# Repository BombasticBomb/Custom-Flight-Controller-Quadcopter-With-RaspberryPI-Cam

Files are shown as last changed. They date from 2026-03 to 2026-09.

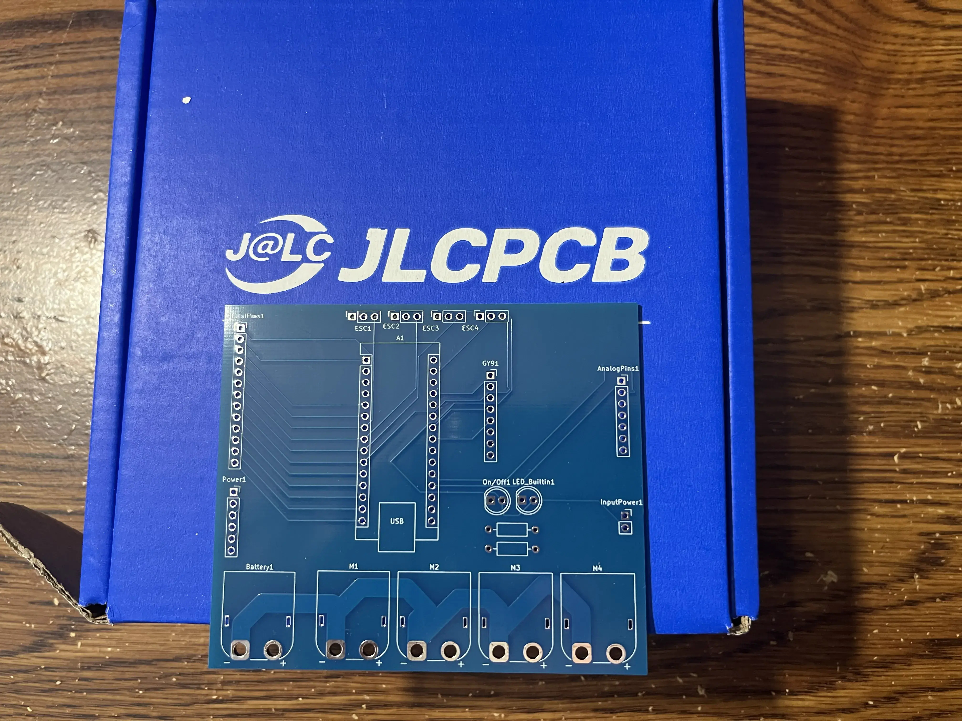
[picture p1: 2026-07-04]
PCB Files/Production/pcb.jpg

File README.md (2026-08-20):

## Custom Drone Flight Controller
Arduino + MPU9250 based Flight Controller for Quadcopter!
This project is a custom-built quadcopter drone that uses an Arduino flight controller with an MPU9250 IMU. Will use a flight controller written in Arduino C++ with a cascaded PID loop for stabilization!
Hack Club Project (Approved): https://stardance.hackclub.com/projects/21695

## 3D Model

This'll be printed in Carbon Fiber Nylon Filament, so it is actually strong enough to be a drone chassis. I will also use a Gyroid infill pattern with 40% infill to make it really strong, and I'll also use a wall count of 6 for further reinforcement. 
parts

## Inspiration
This is my hack club project to build a quadcopter from scratch with a custom flight controller with Arduino &amp; MPU9250. Growing up, I'd watch many science and engineering videos online; I've always been a science kid who spends his time watching astronomy, engineering, etc type videos. I did this project to challenge myself in learning the ins and outs of how a quadcopter actually works, and also to combine my skills in hardware, electronics, and coding to create something unique and not just follow a tutorial.


 ## What Makes This Project Unique
Unlike most custom drones that rely on preprogrammed ready-to-fly flight controllers, my project uses a fully custom flight controller using Arduino & mpu9250 that I had to do a lot of research to actually learn how it works using custom cascaded PID controller loops (and in the future, an extended Kalman filter), and I am working on developing it into a fully functioning firmware. Along with that, I am utilizing a novel method to stream video transmission using a USB camera and the Raspberry Pi using a Python script that uses OpenCV to play video on a web dashboard hosted in Flask and streamed with Flask-socketio. This is a unique method as I offload the low-level control to the Arduino, while I implement advanced features such as a camera (and hopefully in the future GPS, ultrasonic sensors, etc) through the more powerful Raspberry Pi, which actually runs the Linux Operating System.
- Arduino --> Does the low-level flight control and sensor fusion
- Raspberry Pi --> Video Streaming
**Note: Using the onboard wifi on the Raspberry Pi does mean the video transmission range is limited, and beyond that range, we have to rely solely on radio.

## Wiring Diagrams
circuit diagram


| # | Arduino --> MPU9250 | | |
| - | --- | - | --- |
| | **Arduino** | --> | **MPU9250** |
| | 5V | --> | 5V |
| | GND | --> | GND |
| | A4 | --> | SDA |
| | A5 | --> | SCL |

| # | Arduino --> RC Receiver | | |
| - | --- | - | --- |
| | **Arduino** | --> | **RC Receiver** |
| | 5V | --> | 5V |
| | GND | --> | GND |
| | RX | --> | IBus |

| # | Arduino --> ESC | | |
| - | --- | - | --- |
| | **Arduino** | --> | **ESC** |
| | 5V | --> | 5V |
| | GND | --> | GND |
| | 3 | --> | ESC1 |
| | 4 | --> | ESC2 |
| | 5 | --> | ESC3 |
| | 6 | --> | ESC4 |

## Custom PCB:

pcb
Note: The ESCs themselves are part of the wiring diagram and are powered by the Arduino. It is crucial to note the motors themselves, and the Arduino also gets power from the main battery. The reason this configuration was required is that the Arduino converts the 11.1V on the 3S battery to 5V and supplies it to the other electronics.

# Bill of Materials

| Name | Purpose | Quantity | Total Cost (USD) | Link | Distributor |
|---|---|---|---|---|---|
| EVE 50PL 21700 5000mAh 50A Battery | This'll power the drone through its flight. I decided to buy Li-ion batteries and manually connect 3 to make a 3S cell to make a 5000mAh 3S battery pack. This'll help the drone fly longer. I'm buying one extra just in case. | 4 | 24.00 | https://www.18650batterystore.com/products/eve-50pl-21700-5000mah-50a-battery?variant=46405896798359 | 18650 Battery Store |
| JLCPCB Order + Shipping | I'll be manufacturing my custom PCB from JLCPCB. | 1 | 4.30 | https://cart.jlcpcb.com/quote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 | JLCPCB |
| Male & Female Headers | It'll be used to connect things on the PCB. | 1 | 3.82 | https://www.aliexpress.us/item/3256805860047704.html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 | AliExpress |
| XT90 Male to XT60 Female connector for battery | This converts the XT90 on the battery to XT60 so it can be connected to the PCB. | 1 | 1.00 | https://www.aliexpress.us/item/3256809870073827.html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 | AliExpress |
| Drone Frame | This will be the frame that I will be doing all the testing on. I'll have to ship it to my location. | 1 | 5.00 | https://github.com/hackclub/print-legion | Hack Club Legion |
| 1400KV Brushless Motors | These will be the motors that generate lift for the drone. | 4 | 33.40 | https://www.robotshop.com/products/e-s-motor-xxd-a2212-brushless-motor-160w-mounting-base-kits-kv-1400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 | Robotshop |
| Raspberry PI 4 4GB | This will be used to connect the USB camera and for video transmission. I already have this, so I will not need to buy it. | 1 | 0.00 | https://www.centralcomputer.com/raspberry-pi-4-model-b-rpi4-modbp-4gb-4gb-ddr4-ram-bcm2711-soc-usb-3-0-poe-enabled.html | Central Computers |
| Arduino Nano | This will be running the flight software and controlling the motors. I already have this, so I will not need to buy it. | 1 | 0.00 | https://www.aliexpress.us/item/3256809956121978.html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 | AliExpress |
| GY-91 Board with both MPU-9250 & BMP180 | This will the the 9 Axis Flight Controller for the drone (Gyroscope, Accelerometer, Magnetometer, Altometer). | 1 | 6.34 | https://www.aliexpress.us/item/3256810419378175.html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 | AliExpress |
| 8x4.5 Inch RC Drone Propellers | These will be used on the brushless motors to provide lift for the drone. I am buying 8 pieces instead of 4 in case some break during testing. | 1 | 0.92 | https://www.aliexpress.us/item/2251832730802090.html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 | AliExpress |
| 3S Li-po Battery Charger US Plug | This will be used to charge the battery. | 1 | 11.61 | https://www.aliexpress.us/item/3256805934795867.html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 | AliExpress |
| MicroZone MC6C Mini V2 2.4G 6CH Controller Transmitter w/ Receiver | This will be used for the radio communication with the drone. | 1 | 35.24 | https://www.aliexpress.us/item/3256807243819244.html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 | AliExpress |
| 30A Brushless Motor ESC | This will be the Electronic Speed Controller for the 4 brushless motors on the drone. I need to buy 2 pieces for a total of 4 for each motor. | 1 | 12.87 | https://www.aliexpress.us/item/2252799818726193.html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 | AliExpress |
| 12V-5V Buck Converter | This'll convert the 11.1V from the 21700 battery pack to 5V so the Raspberry PI can use it. | 1 | 0.99 | https://www.aliexpress.us/item/3256806059787124.html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 | AliExpress |
| **Total** | | | **139.49** | | |

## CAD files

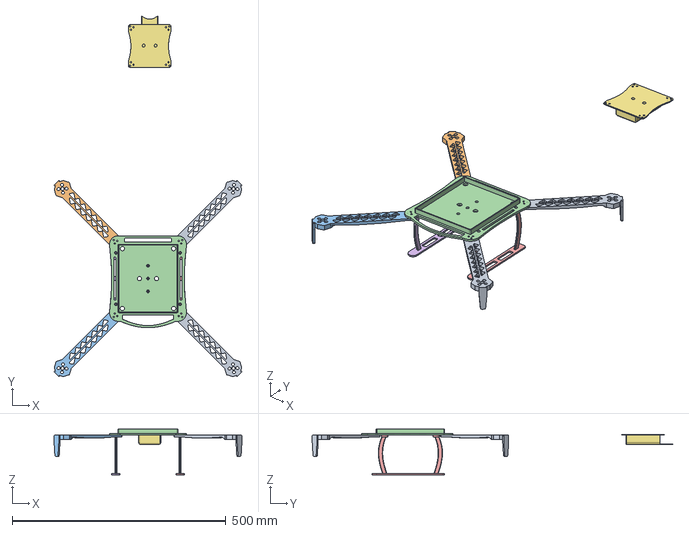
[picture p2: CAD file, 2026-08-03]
CAD/Drone.step
439.9 x 843.9 x 107.0 mm

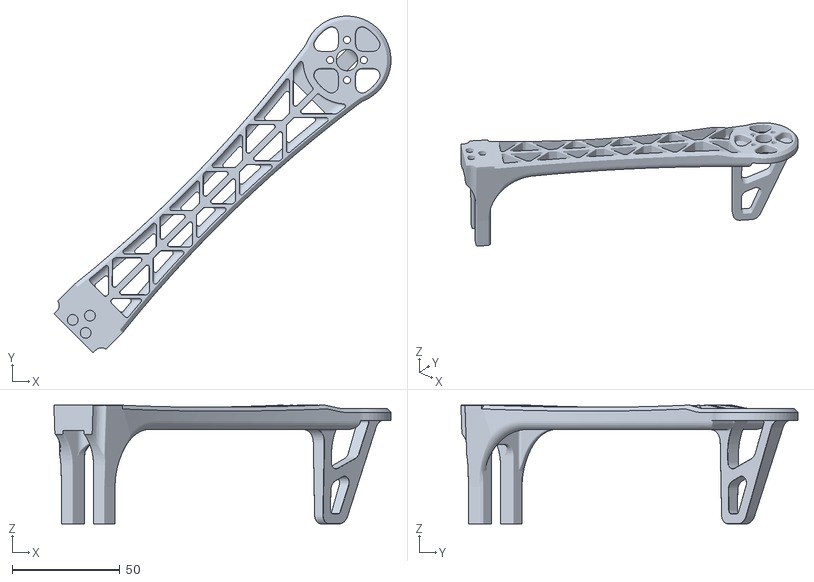
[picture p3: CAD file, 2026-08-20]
CAD/Production/Arm.stl
156.1 x 156.0 x 55.1

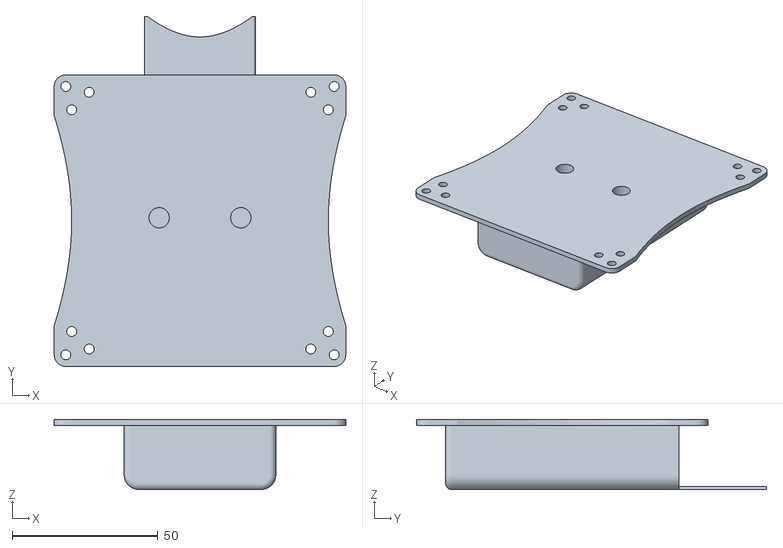
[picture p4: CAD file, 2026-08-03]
CAD/Production/Chassis2.stl
100.0 x 120.0 x 24.0

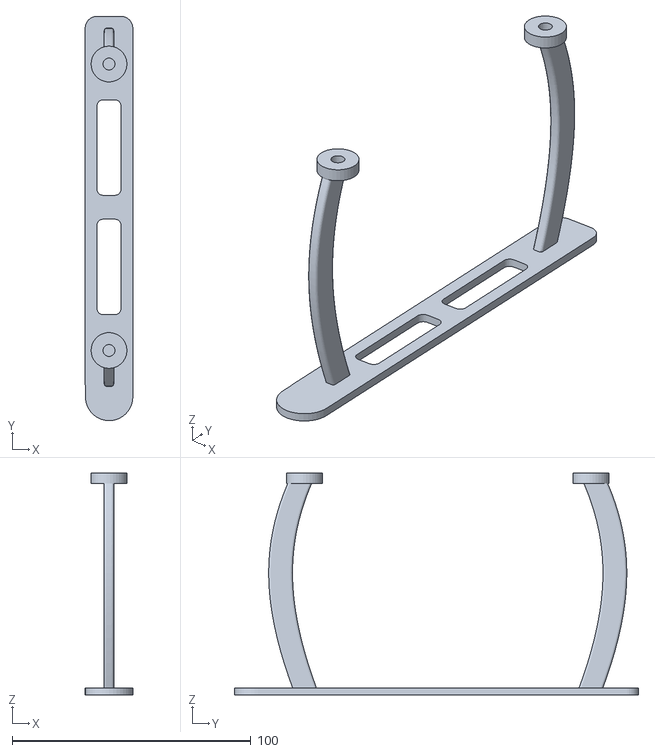
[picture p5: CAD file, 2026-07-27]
CAD/Production/Leg.stl
20.0 x 169.4 x 93.0

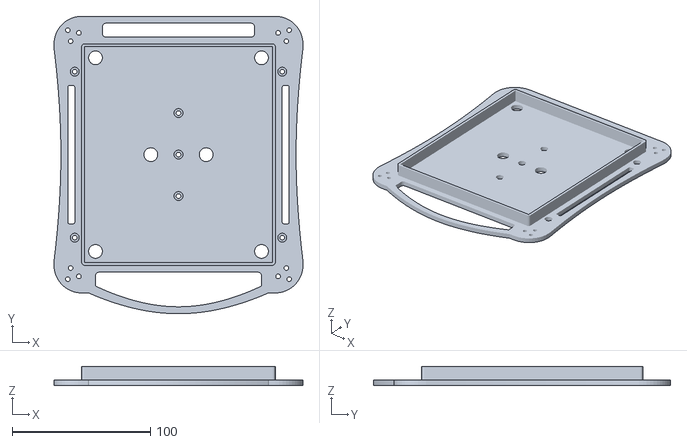
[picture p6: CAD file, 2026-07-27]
CAD/Production/Chassis.stl
180.0 x 215.0 x 14.0

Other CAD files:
CAD/Drone.f3d

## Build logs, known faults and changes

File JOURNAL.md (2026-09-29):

# 9/28/2026 10:32 PM - Setting up F450M Chassis to test brushless motors.

_Time spent: 1h 21m_

Ok, I'm back working on the drone after over a month, I was kinda busy with schoolwork. Anyways, I haven't gotten to test the new arm design, and I called up the printlegion supplier of mine and got a new order going. In the meanwhile, I decided to continue trying to work on the drone with a spare F450 drone chassis kit I had. Not only that, since all my propellers broke last time - lots of work done in this after school session.



Firstly, I screwed together the F450 chassis, unscrewed the motors from my custom chassis and put them on the F450 arms, and it came out as the generic drone everyone builds. Anyways, I also wanted to test if the motors had any thrust imbalances that was causing any problems, as since I crashed the drone a couple of times during previous testing sessions, I feared the motor shafts may have bent. Therefore, this test can validate the motors with a tried and tested chassis before I go back to my original chassis.



After that, I obviously attached the new propeller sets I got. Before I was testing out in the roads on concrete, so each crash ended up breaking 1 or 2 propellers. So, this time I not only got new stronger propellers that had a larger pitch and a stronger mid-section, I am also thinking of doing all my testing in the grassy area nearby, so hopefully no more propellers will break.



Lastly, I am realizing the cascaded pid loop I am running on the arduino may be too slow, as the arduino is not a very powerful microcontroller. So, my next target is now an ESP32, as the advanced control features I want to implement needs a stronger processor. Not only that, the ESP32 also has a built-in FPU, which should make my PID calculations much faster. But before I start migrating my code however, I again want to test my motors, and so for now I decided to test the drone with ESP-FC, an open source drone firmware for ESP32 that is configurable with betaflight configurator.



I flashed it and got betaflight configurator running, but I didn't get any chance to set up the pins. One advantage of using ESP32 is that it has hardware interrupts on many GPIO pins, and it can also use the SBUS protocol my receiver uses instead of individual PWM channels. Next session I'll set up all the pin connections, PID tune betaflight, and hopefully there'll be no problems with my motors.

# 8/19/2026 8:39 PM - Designing New Arm.

_Time spent: 54m_

Today I decided to tackle the problem of designing a completely new arm for the drone. As I already mentioned before, the arm keeps getting bent from the thrust and also the weight of the drone, meaning I'd need to make it stronger and more stiff so it doesn't bend.


So I started designing, but since I was designing on a pretty cluttered design file and my arm was built up with work over many days, what I designed was not something I particularly liked.

This project was getting more time-consuming and expensive than it ever needed to be, and it was getting bad. I struggled with this for like about 30 minutes, but I couldn't find ways to quickly make it better, and now that school had started I didn't have time like before to iterate and reprint quickly.
So, I took a shortcut, I had to...

I decided that in order to save time, atleast for the arm, I'd go with the tried and tested DJI F450 arm design, and make some small designs to make it work with my specific chassis.
Using the holes from my chassis, I cut those holes into the new arm design so I can attach it with M3 screws to the main chassis.
Therefore, credits to Sarthak Nashirabadkar on GrabCAD for the arm design, it really helped me to quickly get this project back on its feet.
Link: https://grabcad.com/library/f450-quadcopter-drone-frame-1



Additionally, I also made another small attaching thing in case someone want to use actual DJI F450 arms, and just 3D print their chassis, and so for that reason I made a small adapter to attach that arm to my chassis.


Lastly, I also made the legs of the drone a little thicker, as the last time I printed it they were way too thin and broke on the first day.


# 8/18/2026 8:34 PM - Testing 1st Flight (Failed).

_Time spent: 1h 37m_

Today I tried to do my first test run. Firstly I connected up the propellers and saw if the motors spin properly. Then, I went in and tried to see if the drone could stabilize with my code.


Then, I tried to test run it on a weight I had lying around to see if it could stabilize. But no matter what, it just won't stabilize. The drone would like shake up and down for some reason on both sides.

So then I tried tweaking the values by increasing the rate pid constants and decreasing the angle one. It didn't help much. 

So, I tried installing ESP-FC on my ESP32, which is a community made ready-to-fly flight controller, to just see if there's something seriously wrong with my hardware.

Due to the ESP-FC being reall good firmware the drone was able to stabilize better, but it seems like my arms were getting bent by the sheer weight and the thrust. Apparently it was a structural issue all along!


Therefore, I decided to not waste any more time on this drone and get back to designing. I'll be soon designing a new drone arm and getting that printed, and hopefully this time it'll be much thicker and do fine.


# 8/11/2026 6:46 PM - Assembling The Parts.

_Time spent: 1h 07m_

I finally got the 3D printed chassis parts for my drone, and I wasted no time and got to work assembling it. Here's some individual photos.



I used M3 screws, bolts and washers. The arms are a bit loose, but we'll see.

# 8/1/2026 4:36 PM - Redesigning Drone Mounting Holes

_Time spent: 2h 05m_

I was hesitant to print the drone arm without testing them with the actual motor first, so I printed one.



However, I soon realized that even though from google I found that these motors have a mounting pattern or 16mmx19mm, the actual dimensions were definitely off on my specific motor brand, as I couldn't get it to fit at all. The holes had also shrunk due to the printing layers.


After some back and forth on my Ender 3 Pro, I realized the best dimension was actually 12.7mm x 13.5mm, which is wildly different from the actual one. Anyways, I also decided to use a custom hole and not the designated M3 hole in fusion 360, and I'll just use washers to make sure the screws stay where they are and look clean.




And, it finally worked!



# 8/1/2026 4:36 PM - Updating PID Controller to Cascaded PID Loop

_Time spent: 3h 03m_

First of all, it seems like I got scammed on the GY-91 chip I bought from Aliexpress, cause the chip returns a WHO_AM_I address of 0x70, which is the address of the MPU6500, not the MPU9250 I ordered. I did some more research, and it seems like these chinese sellers often put those chips and call it MPU9250. Thus, I won't be able to use a magnetometer to correct yaw drift, but hopefully I'll buy a good proper IMU from Adafruit or something, but that'll be for a future upgrade when I also move to the ESP32.

Anyways, I went on and implemented a cascaded pid loop in my code. The inner loop is faster and controls angular velocity, which keeps the drone stable. In my code, I allowed the inner loop to run as fast as possible, and then the outer loop runs. My overall loop has a set HZ rate of 500HZ, but let's see if the Arduino can actually run that fast.



Sadly to add on to my problems, I also got stuck with the issue that the Mahony filter didn't work no matter what I did. Since I didn't read into the implementation of the filter in the library, and it'll be too complicated, I decided to switch back to a complementary sensor fusion algorithm. I took 95% from the gyroscope, and 5% from the accelerometer. It won't have noise correction, but I think it'll do for now. And obviously I don't have any yaw correction. 


For the angles from the accelerometer, I used atan2 function to get the angles, and in the code I didn't use g and rather took the vector of the az and ay component using pythagorean theorem. Originally I thought I could use gravity g, but since the drone experiences g forces we can't use it.


For the Gyroscope I took the rates in radians, converted them to degrees by multiplying them by 180/pi, and then took the current angle and to that I added the Gyro rates multiplied by dt, essentially integrating the gyro rates over time to get the angles. This was done in the complementary filter.


To correct gyro bias, I made a small section of code to sample the gyroscope a set amount of times, for example 4000 samples, and average them and subtract them from the gyroscope data to find the true angles, or as close as possible. With this however, it adds a 1-2 second delay to the startup time, but I think it's definitely worth it as now the Gyroscope will adjust and calibrate no matter what happens to the drone structurally.


Lastly added some flight mode code and a flight variable so the drone knows whether its in flight mode or not.


In the next part of the code I'll probably try to replace the ServoTimer2 library with my own implementation of PWM signals, as it may cause problems because of the pin timer. Also after I get the frame I also have PID tuning to do.

# 8/1/2026 1:25 PM - Soldering the Drone Battery

_Time spent: 3h 13m_

Confident after soldering the last batch of batteries. I decided to start soldering the RS50 Reliance batteries I bought for the actual drone. It started of really rough, with me burning my hands a couple times. So I tried like last time to not use flux, which improved a little bit, but not enough to make it work. Then, I finally ran out of solder, which made me open my new pack of solder I bought. And miraculously, the solder started working. I realized that this new solder had a flux core, which made my life way more easier, and I was able to finish soldering all the batteries.

I hooked it up to my Arduino and ESC, and it was providing nice power.



Just to be sure, I also measured the voltage of the batteries, and since they were almost fully charged, they showed 12.3V, which is normal for a 3S cell.


I also connected it to the smart charger after attaching the load balancing wires, and the 3 cells were all charging normally.


# 7/27/2026 3:40 PM - Designing a second low-profile Chassis for Drone.
I wanted to add a smaller low-profile chassis for the drone if I ever fly it with no big landing legs or payload or cameras, and so I designed another chassis that I'll also manufacture soon.




# 7/24/2026 10:58 PM - Soldering 1st batch of batteries.

_Time spent: 2h 26m_

Today, my order from 18650 battery store for 3 21700 Li-ion cells came in. These are very beefy cells with a max pulse current of 70A and 5000mah capacity, so should be more than enough for my drone project. 

But, since I've never soldered batteries together before and I can't afford a spot solder right now, I decided to test solder on some old 18650 cells I had, and that's what I did.

Overall, it started off pretty rough as the solder was not sticking to the ends of the cells no matter what I tried. Then, i figured that it worked better if I didn't use any flux, which'd to me was counterintuitive as flux makes the solder stick. But anyways, I tried without and managed to solder all the wires together, and it gave me a nice 12V on the 3S cell.

To interface with the smart charger I also bought, I also attached a 4 pin connector to the battery for load-balancing smart charging. Overall it works great and the charger can individually tune the voltages of each cell for protection.


Hopefully in the next log I'd be able to finish soldering the actual 21700 cells to make another, much beefier pack that I'll actually use on the drone. This was for first-time practice and getting to actually know how its done!

# 7/23/2026 7:29 PM - Added Secondary Landing Legs.

_Time spent: 3h 21m_

Firstly, I decided to write the Motors mixer function for the drone with a standard Quad X setup, so I can just call it in the main loop and it'll update the motor values on each iteration according to the PID values.



Then, I write a simple PID function that I'll be using in the main loop. This is not yet a cascaded PID controller, but it's a start. I made some state variables and wrote the function to add up the proportional, integral and derivative part.


To then feed data into the PID function, I used the BolderFlight Invensense Arduino library to interface it with the MPU9250, and get all the data.



All IMU sensors have noise in the data, but since an Arduino is a relatively weak microcontroller running at only 16Mhz, I decided to use a light filter called a Mahony filter, and used the MahonyAHRS library to implement it in my code. If i ever upgrade the flight controller hardware, I'll then manually implement a Extended Kalman Filter, but right now it is too expensive for the Arduino.


I also decided to set the PID loop at a 500Hz rate, which is also how I calculated dt in my code.


Finally, I made a PID controller for each axis of the drone and ran the mixer function at the end of the loop. Also made it that the integral portion will go to 0 when the drone is on the ground to prevent integral buildup when the drone is stationary.


# 7/21/2026 11:34 PM - Added Secondary Landing Legs.

_Time spent: 57m_

I added some small DJI Mini style landing legs to the drone, so that if I ever want I can take the big landing legs off and just have a low profile setup.




# 7/20/2026 10:28 PM - Started writing code to interface the Arduino with the RC transmitter.

_Time spent: 2h 47m_

Firstly, I decided to do some research about the channel configuration and how to read PWM signals from the receiver. Originally, I thought I was going to use the IbusBM library, but apparently my receiver didn't support it.


To solve this problem, I thought I'd use Arduino Nano's hardware interrupts, but the Nano only had 2 pins, and I needed a minimum for my 4 channels: Throttle, Pitch, Yaw, and Roll. Then, I found out about something called pin change interrupts, but those required manual memory address and pin registry configuring, and thankfully the Arduino PinChangeInterrupt library took care of that for me.


Not only that, but I also found out that RC transmitters like these don't have perfect PWM signal outputs, as I measured with the arduino. To fix that and scale it to the perfect 1000um-2000um range needed for the ESCs to work well, I decided to log the range of values that each of the 4 channels output, and used the arduino map() function to scale it to the desired range and constrained it with the constrain() function. This worked remarkably well and I tested it with a Brushless motor and it worked well.



# 7/19/2026 18:03 PM - Completely changed the thickness of parts as Carbon Fiber Nylon is strong enough, and added many decoration holes and patterns to vastly reduce weight.

_Time spent: 3h 19m_


I added these design holes found in other drone chassis kits that not only made it look nicer, it reduced a lot of weight without making the arms that much weaker, as carbon fiber is a very strong material. This reduced the weight of the individual arms from 37g to 25g, as per the printing settings I used. 


Also added some cutouts to the chassis that didn't drastically reduce weight, as the chassis is relatively thin. However, this'll allow me to tie things onto the drone if I ever need to do so in the future, and it also looks nice on the drone chassis.


Similarly, added cutouts to the bottom legs and thinned the pads out a bit too to reduce weight. This resulted in almost 50g of weight reduction.

chip
I was having anxiety about flexing where the motor attaches to the arms, so I made it thicker at just that part. I also added a smooth hilly part that should make it really strong.

# 7/16/2026 9:38 PM - Added Superior Landing Legs & Added Extra Mounting Holes (Future Development)

_Time spent: 2h 34m_


I added 2 extra mounting holes so I can add on new modules in the future for items like Gimbal Camera, GPS, Drop mechanism, etc.


The previous landing leg design had a center of gravity that was relatively high, and standing on tiny legs with little surface area. This design fixed it by making the legs shorter, and adding a smooth pad at the bottom
that'll also be reinforced with shock absorbing foam. Even added some tall standoffs on the arms that may or may not allow me to completely take of the landing legs and land on those!

# 6/26/2026 10:25 PM - Switched Flight Controller From MPU6050 to MPU9250

_Time spent: 21m_


Updated Flight Controller Code for MPU9250 Since I previously tested and wrote code with a MPU6050 because I physically had the sensor, I now decided to update the code to the new and more advanced 
MPU9250. Today’s session was mostly about getting the sensory data (Roll, Pitch, Yaw) from the sensor, and I haven’t implemented a PID loop yet, and I’ll focus on that next, as well as implementing the 
connections from the custom PCB.


# 6/19/2026 1:30 PM - Added Smooth Underside to the Arm and added Electronics Housing

_Time spent: 22m_


I made the arms of the drone thicker so it is more resistant to crashes, which may happen quite a bit during initial PID tuning and testing.

Not only that, I also added a small cutout on the top to house the main electronics, including the battery, the Raspberry PI, and also the custom PCB.


# 6/11/2026 9 PM - More changes to the 3D model of the Drone

_Time spent: 1.5h_

Today, I completely redesigned the chassis of the drone to better suit my needs, as the previous one was too small.


Kept the drone mounting holes the same for the brushless motors, but for simpler building also added screw holes for the 4 arms to attach to the main body.

Also further tweaked the brushless motor part.


In the bottom, added landing legs to provide better stability.



To house the electronics, I added a small area on the top to hold the parts.


# 6/10/2026 10 PM - Designing New Drone Chassis

_Time spent: 2.5h_

In this session, as per the instructions, I decided to make a more stable version of the drone, and this time, it will be fully 3D printed in carbon fiber instead of aluminium to save costs. Since my 3D printer can't print carbon fiber, I will be using Hack Club PrintingLegion. 

For the main drone body, I took inspiration from this YouTube video. 
Link: https://www.youtube.com/watch?v=jeBfLHX1kos&t=72s

However, that'd not fit my requirements, so I will also be adding proper M3 holes and a through-hole for my Bushless motors, and this video helped a lot.
Link: https://www.youtube.com/watch?v=4bDNXpWQaW4


Lastly, I think I'll make some more changes to the drone to make it even sturdier, like adding some pressure absorbers at the bottom of the legs.

# 4/18/2026 6 PM - Finish Designing Custom PCB

_Time spent: 2.5h_

While I was working on the PCB, I decided it's out of my scope to use bare metal chips for the sensors, so in order to improve electronic noise and have a better chance of the PCB working, I decided to switch out the sensor chips for modules. 

Also, due to size constraints, I decided to go with Arduino Nano instead of the big Arduino UNO, as it better fits the PCB. For future developments, I also added lots of header pins connected to the digital and analog pins on the Arduino, so I can expand my capabilities in the future. Similarly, I also added some power pins to power those sensors.

Lastly, I made the PCB and made all the traces. I went with thicker 4mm traces for the Motor power distribution, as more current will flow through them, and everything else with normal 0.025mm traces.

Here's the final PCB:


# 4/7/2026 3 AM - Flight Controller PCB V1

_Time spent: 2h_

I decided to start working on a custom PCB because, without it, the complexity isn't high enough. This is my first time making a custom PCB, so I gave it my best shot :)


I decided to use KiCad for this, and I used bare chips instead of modules for now. Apparently, there are a lot of issues with electronic noise for quacopter PCBs, so I had to do a lot of research on where and how to place components. And, for better sensor readings, I also had to put a 10K resistor, decoupling capacitors, and a MOSFET for level-shifting.


Still not sure whether I will continue this setup, as the electronic noise is a big deal. Might end up switching that out for the GY-91 module itself.

# 3/23/2026 3 AM - PID Loop V1 (Stabilization)

_Time spent: 1h_

In order for a drone to be stable, it needs a feedback loop system that constantly tries to keep it stable, thus keeping its angle 0*. One industry standard way is to implement a PID loop. A PID loop consists of 3 different parts: the proportional, the integral, and the derivative, and the PID controller is the sum of all these 3 controllers. I plan to create a PID controller for each dimension of the drone.

Source: https://en.wikipedia.org/wiki/Proportional%E2%80%93integral%E2%80%93derivative_controller

After some research on YouTube about how a PID controller works, I tried creating my own loop in the stabilization part of my firmware and called the stabilize() function which has the controller. As of right now, I don't have much of an idea as to how the motors behave and how much thrust increases as I increase speed in percentage, so I just made it increase and decrease thrust based on the values from the PID loop. When I actually build the physical drone, it'll have the PID constants tuned, and I'll also tune the thrust increase/decrease for optimal flight.


# 3/19/2026 4 AM - Basic Gyroscope & Accelerometer Sensor Fusion along with Throttle Control

_Time spent: 3.5h_

After choosing the parts for the drone, I decided to start working on the flight controller. In my previous journal logs, I've already shown getting the gyroscope roll, pitch, and yaw values, but as I learned during my research, the gyroscope is subject to drift. The solution - fusing data from the gyroscope along with roll and pitch values gained by integrating the angular velocity given by the accelerometer to get angles, with the gyroscope contributing 98%, while the accelerometer 2% for corrections.


The yaw values cannot be corrected as it would require a magnetometer, which I will use in the final build by replacing the MPU6050 with an MPU9250. 


I also started writing code for reading signals from the radio receiver and its corresponding actions on the motors, which I've defined as servos in the code.
Channels



# 3/18/2026 4 AM - Designing 3D Model of Drone

_Time spent: 2h_

In the past 2 hours, I designed the basic 3D outline of the drone in TinkerCAD to be approved by Hack Club. I chose the parts that I will be using and looked for 3D models online, and if I found them, I used them in the design. Otherwise, I tried to mimic the actual part with TinkerCAD shapes and labels. Things to note: this may be subject to change as I build the project and make important decisions.


If looking for my 3D model to review and approve my project, please look in the releases section. Due to the large file size of the .step file when extracted from the original STL file, it had to be uploaded to releases. 


# 3/17/2026 9 PM - Deciding Propeller, Motor & Battery Sizes

_Time spent: 3h_

In this session, I finished researching the different configurations for the drone and chose the most efficient for my purpose. I decided to stick with 1400kv Brushless motors for a good balance between speed and efficiency, and chose 4 pieces to buy on Amazon.

Then, I chose a 4000mAh 3S Li-po battery for a good flight time and also 4 30A ESCs separately for a better price. Ended up with an 8x4.5 propeller size for the final drone.

Finally, started working on choosing a frame for the drone. I am not sure whether I should buy a frame or print one on my 3D printer, but let's see.

Considering this one:

Source: https://www.printables.com/model/250067-drone-frame

# 3/17/2026 4 AM - Choose Parts

_Time spent: 2.5h_

In the last 2 and a half hours, I brainstormed ideas as to how to build the drone in real life, and decided to choose electronics parts for each job. I decided to go with 1400KV brushless drone motors along with 30A ESCs, along with a radio controller and transmitter for communication. I decided to build a custom IMU with Arduino and MPU6050, and I haven't decided yet on how to build the structural part of the drone. I also started tinkering with the MPU6050 to start building the PID controller for the IMU. 





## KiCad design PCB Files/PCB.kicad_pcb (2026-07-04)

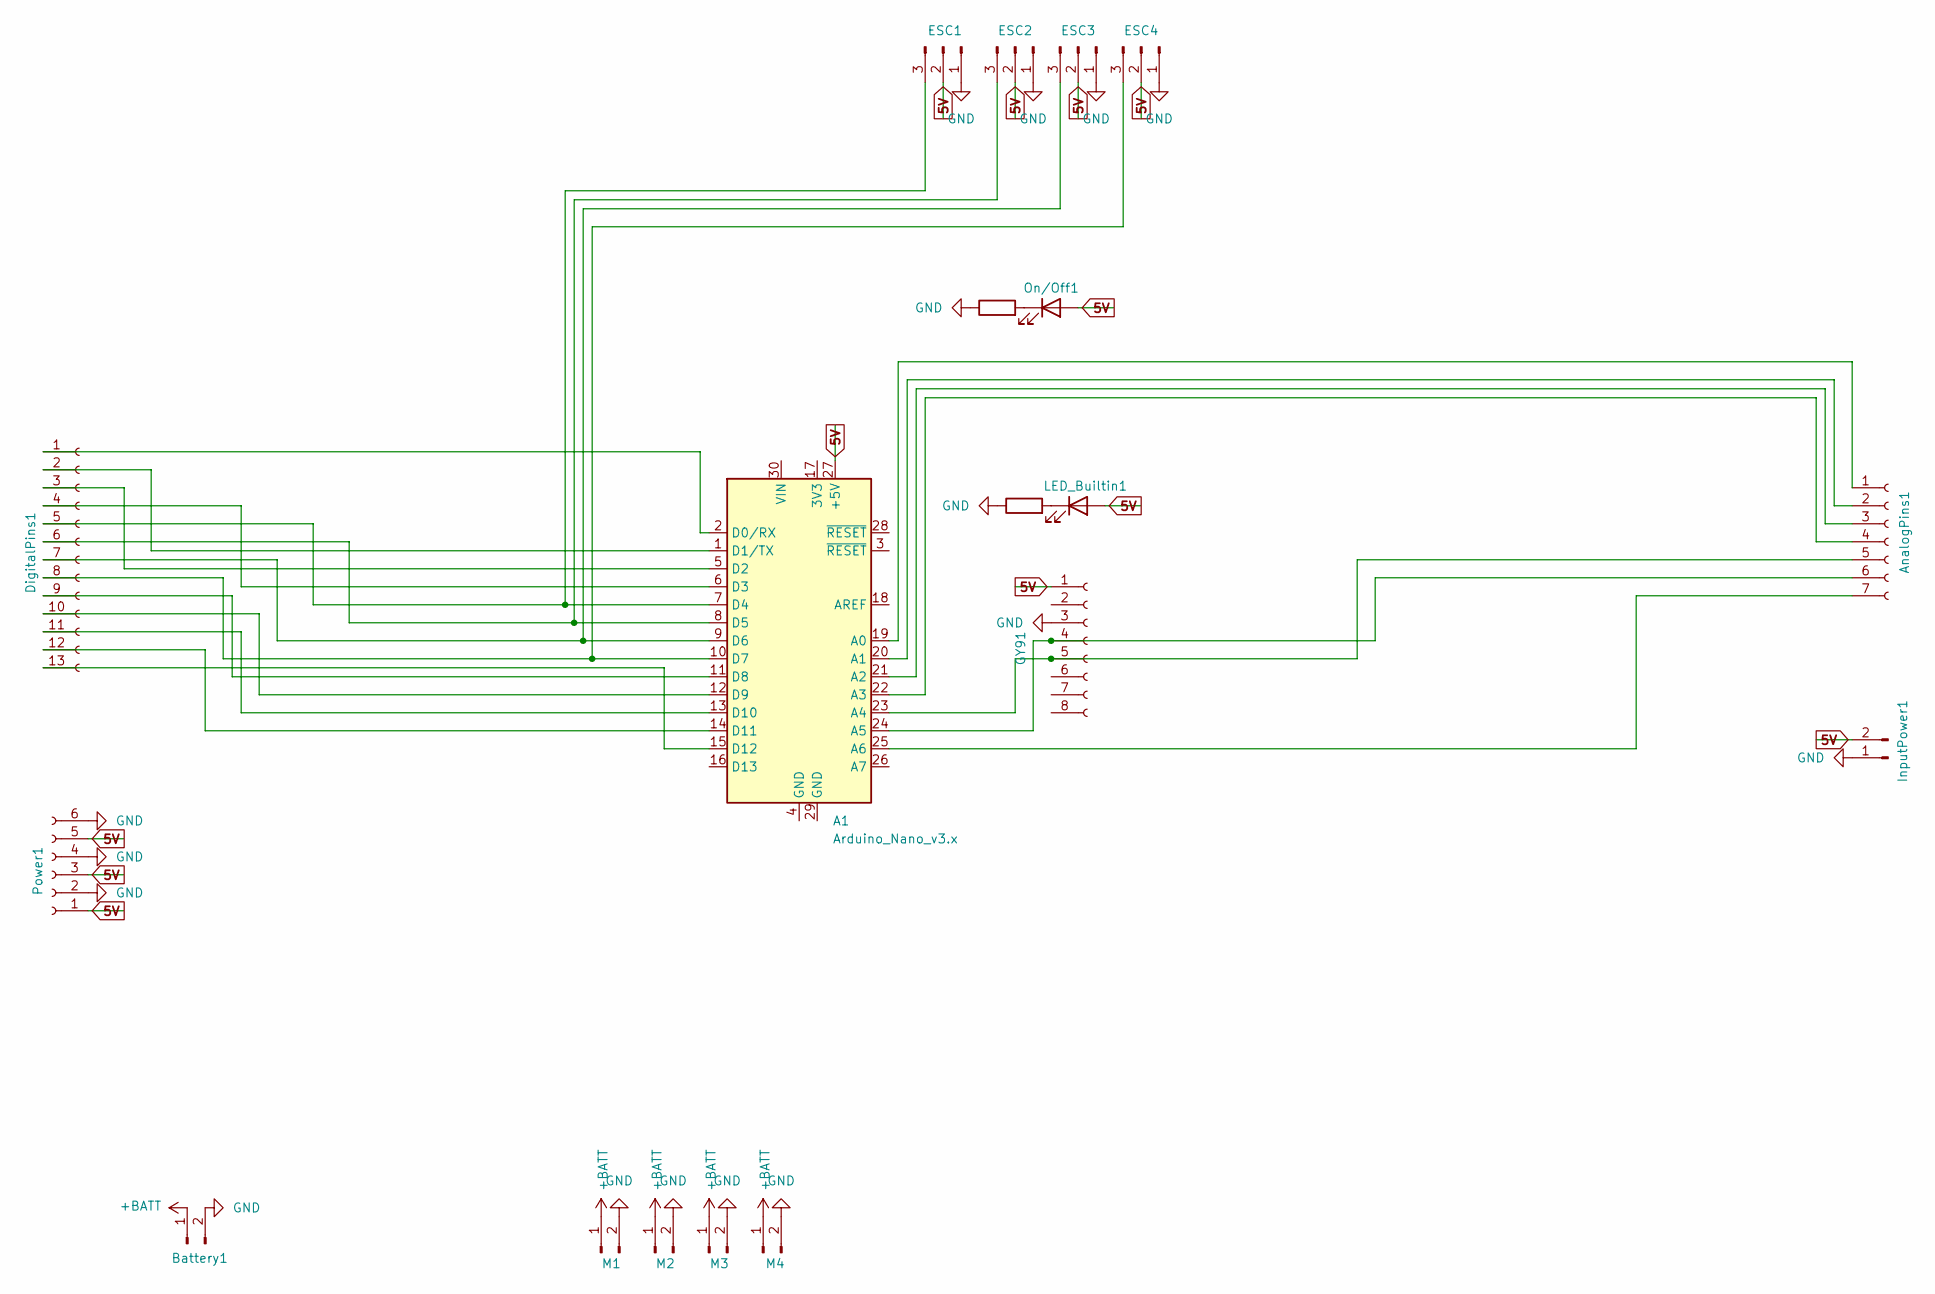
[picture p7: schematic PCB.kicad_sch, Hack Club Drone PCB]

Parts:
A1: Arduino_Nano_v3.x; Arduino_Nano
AnalogPins1: Conn_01x07_Socket; PinSocket_1x07_P2.54mm_Vertical
Battery1: Conn_01x02_Pin; AMASS_XT60PW-M_1x02_P7.20mm_Horizontal
DigitalPins1: Conn_01x13_Socket; PinSocket_1x13_P2.54mm_Vertical
ESC1, ESC2, ESC3, ESC4: Conn_01x03_Pin; PinSocket_1x03_P2.54mm_Vertical
GY91: Conn_01x08_Socket; PinSocket_1x08_P2.54mm_Vertical
InputPower1: Conn_01x02_Pin; PinSocket_1x02_P2.54mm_Vertical
LED_Builtin1: LED; LED_D5.0mm
M1, M2, M3, M4: Conn_01x02_Pin; AMASS_XT60PW-M_1x02_P7.20mm_Horizontal
On/Off1: ON/OFF; LED_D5.0mm
Power1: Conn_01x06_Socket; PinSocket_1x06_P2.54mm_Vertical
R220-1, R220-2: 220; R_Axial_DIN0207_L6.3mm_D2.5mm_P10.16mm_Horizontal

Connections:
5V: A1.27 (+5V), ESC1.2, ESC2.2, ESC3.2, ESC4.2, GY91.1, InputPower1.2, LED_Builtin1.2 (A), On/Off1.2 (A), Power1.1, Power1.3, Power1.5
+BATT: Battery1.1, M1.1, M2.1, M3.1, M4.1
GND: Battery1.2, ESC1.1, ESC2.1, ESC3.1, ESC4.1, GY91.3, InputPower1.1, M1.2, M2.2, M3.2, M4.2, Power1.2, Power1.4, Power1.6, R220-1.1, R220-2.1
unnamed: A1.19 (A0), AnalogPins1.1
unnamed: A1.20 (A1), AnalogPins1.2
unnamed: A1.21 (A2), AnalogPins1.3
unnamed: A1.22 (A3), AnalogPins1.4
unnamed: A1.23 (A4), AnalogPins1.5, GY91.5
unnamed: A1.24 (A5), AnalogPins1.6, GY91.4
unnamed: A1.25 (A6), AnalogPins1.7
unnamed: A1.2 (D0/RX), DigitalPins1.1
unnamed: A1.1 (D1/TX), DigitalPins1.2
unnamed: A1.5 (D2), DigitalPins1.3
unnamed: A1.6 (D3), DigitalPins1.4
unnamed: A1.7 (D4), DigitalPins1.5, ESC1.3
unnamed: A1.8 (D5), DigitalPins1.6, ESC2.3
unnamed: A1.9 (D6), DigitalPins1.7, ESC3.3
unnamed: A1.10 (D7), DigitalPins1.8, ESC4.3
unnamed: A1.11 (D8), DigitalPins1.9
unnamed: A1.12 (D9), DigitalPins1.10
unnamed: A1.13 (D10), DigitalPins1.11
unnamed: A1.14 (D11), DigitalPins1.12
unnamed: A1.15 (D12), DigitalPins1.13
unnamed: LED_Builtin1.1 (K), R220-2.2
unnamed: On/Off1.1 (K), R220-1.2

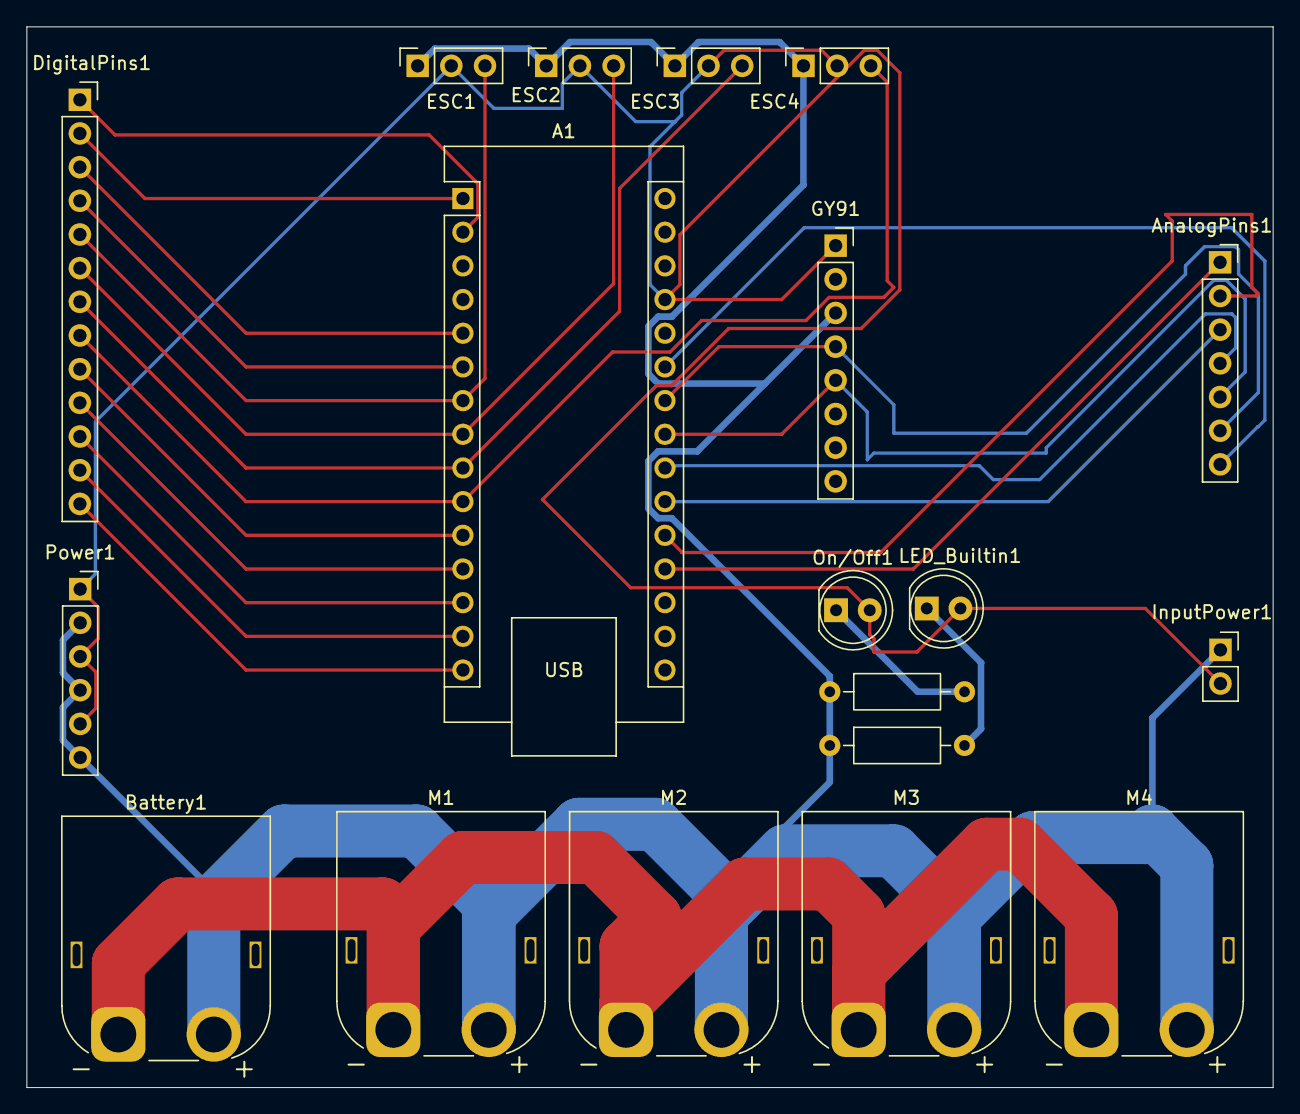
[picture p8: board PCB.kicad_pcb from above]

Board: 2 copper layers, 94.0 x 80.0 mm, 19 parts (0 on the bottom side), 25 nets.

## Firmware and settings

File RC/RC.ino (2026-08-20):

/*
 *Throttle - (944,1944)
 *Pitch - (1196,1694)
 *Yaw - (1248,1752) 
 *Roll - (1296,1800)
 
 *Throttle = Up or Down (Channel 3)
 *Pitch = Forward or Backward (Channel 2)
 *Yaw = Rotation (Channel 4)
 *Roll = Left or Right (Channel 1)
 */

#include "PinChangeInterrupt.h"
#include <Servo.h>
#include "mpu6500.h" //I got fucking scammed so i now gotta use mpu6500 instead of mpu9250!!!

//Flight state variables
bool flight = false;
char flightMode;
float maxFlightSpeed = 0;

//Variables
const int throttlePin = 2; volatile unsigned long throttlePWMStart = 0; volatile int throttleTemp = 1000; 
const int pitchPin = 3; volatile unsigned long pitchPWMStart = 0; volatile int pitchTemp = 1000;
const int yawPin = 4; volatile unsigned long yawPWMStart = 0; volatile int yawTemp = 1000;
const int rollPin = 5; volatile unsigned long rollPWMStart = 0; volatile int rollTemp = 1000;
int minPWM = 1000; int maxPWM = 2000;
int minTilt = -20; int maxTilt = 20; //Tilting of the drone
float currentPitchAngle = 0.0; float currentYawAngle = 0.0; float currentRollAngle = 0.0;
float ax; float ay; float az; float gx; float gy; float gz; float mx; float my; float mz;

//Loop frequency regulation
float loopRate = 500.0; //Loop rate in Hertz (Hz)
const unsigned long refreshInterval = 1000000 / loopRate; // 2000 microseconds
unsigned long previousMicros = 0;

//MPU9250 & BMP280
int imuCSPin = A0;
int bmpCSPin = A1;
bfs::Mpu6500 imu(&SPI, imuCSPin);

//Transmitter Ranges
int throttleStart = 944; int throttleEnd = 1944;
int pitchStart = 1196; int pitchEnd = 1694;
int yawStart = 1248; int yawEnd = 1752;
int rollStart = 1296; int rollEnd = 1800;

//---PID Variables---
//Pitch Angles & Rate Varibales
float pitchAngleKp = 2.0f; float pitchAngleKi = 0.00f; float pitchAngleKd = 0.0f;
float pitchAngleIntegral = 0.0f; float pitchAngleLastError = 0.0f;
float pitchRateKp = 1.0f; float pitchRateKi = 0.00f; float pitchRateKd = 0.0f;
float pitchRateIntegral = 0.0f; float pitchRateLastError = 0.0f;
//Roll Angles & Rate Variables
float rollAngleKp = 2.0f; float rollAngleKi = 0.00f; float rollAngleKd = 0.0f;
float rollAngleIntegral = 0.0f; float rollAngleLastError = 0.0f;
float rollRateKp = 0.75f; float rollRateKi = 0.00f; float rollRateKd = 0.0f;
float rollRateIntegral = 0.0f; float rollRateLastError = 0.0f;
//Yaw Angle 
float yawAngleKp = 0.5f; float yawAngleKi = 0.00f; float yawAngleKd = 0.0f;
float yawAngleIntegral = 0.0f; float yawAngleLastError = 0.0f;
//Storage variables
const float dt = 1.0 / loopRate; int pidPitch = 0; int pidYaw = 0; int pidRoll = 0;
const float pidPWMMin = -450; const float pidPWMMax = 450;

//Sensor fusion variables
float gyroPitch = 0; float gyroYaw = 0; float gyroRoll = 0;
float accelPitch = 0; float accelRoll = 0;
float radToDeg = 57.2957795f; 
float gxBias; float gyBias; float gzBias;
float axBias; float ayBias; 
const int numSamples = 4000; //Bias correcting samples
int successfulSamples = 0;

//Define Motors
Servo esc1; int esc1Pin = 6;
Servo esc2; int esc2Pin = 7;
Servo esc3; int esc3Pin = 8;
Servo esc4; int esc4Pin = 9;
bool motorsEnabled = true;


void setup() {
  Serial.begin(115200);
  SPI.begin();

  //Set the pins as input
  pinMode(throttlePin, INPUT);
  pinMode(pitchPin, INPUT);
  pinMode(yawPin, INPUT);
  pinMode(rollPin, INPUT);
  
  //Set the CS pin on GY-91 to input, as I'm using analog pins as I ran out of digital IO
  pinMode(imuCSPin, OUTPUT);
  digitalWrite(imuCSPin, HIGH);
  pinMode(bmpCSPin, OUTPUT);
  digitalWrite(bmpCSPin, HIGH);

  // Initialize the MPU9250
  if (!imu.Begin()) {
    Serial.println("Error initializing communication with IMU");
    while(1) {} // Halt if sensor not found
  }
  // Configure internal Digital Low Pass Filters (DLPF)
  imu.ConfigAccelRange(bfs::Mpu6500::ACCEL_RANGE_16G);
  imu.ConfigGyroRange(bfs::Mpu6500::GYRO_RANGE_2000DPS);
  imu.ConfigDlpfBandwidth(bfs::Mpu6500::DLPF_BANDWIDTH_184HZ);

  //Using the Arduino PCINT Library, it is a pin change library
  attachPCINT(digitalPinToPCINT(throttlePin), readThrottle, CHANGE); 
  attachPCINT(digitalPinToPCINT(pitchPin), readPitch, CHANGE);
  attachPCINT(digitalPinToPCINT(yawPin), readYaw, CHANGE); 
  attachPCINT(digitalPinToPCINT(rollPin), readRoll, CHANGE); 

  //Attach and Arm ESCs
  esc1.attach(esc1Pin); 
  esc2.attach(esc2Pin); 
  esc3.attach(esc3Pin); 
  esc4.attach(esc4Pin);

  //Zero throttle for stopping
  esc1.writeMicroseconds(minPWM);
  esc2.writeMicroseconds(minPWM);
  esc3.writeMicroseconds(minPWM);
  esc4.writeMicroseconds(minPWM);

  // Calibrate gyro bias 
  while (successfulSamples < numSamples) {
    if (imu.Read()) {
      gxBias += imu.gyro_x_radps();
      gyBias += imu.gyro_y_radps();
      gzBias += imu.gyro_z_radps();

      axBias += imu.accel_x_mps2(); 
      ayBias += imu.accel_y_mps2(); 
      successfulSamples++;
    }
    delayMicroseconds(250);
  }
  gxBias /= numSamples;
  gyBias /= numSamples;
  gzBias /= numSamples;

  axBias /= numSamples;
  ayBias /= numSamples;
   
  delay(2000); //Wait 2 seconds for arming

  // Initialize clock timing anchor right before entering the loop
  previousMicros = micros(); 
}

void loop() {
  unsigned long currentMicros = micros();

  //500Hz loop
  if ((currentMicros - previousMicros) >= refreshInterval){
    
    // Safety check: if we fell behind by more than 5ms, reset anchor to avoid death spiral
    if ((currentMicros - previousMicros) > 5000) {
      previousMicros = currentMicros;
    } else {
      previousMicros += refreshInterval;
    }

    //Set flight mode
    setFlightMode('S');
    

    //Set no interrupt to not corrupt data
    noInterrupts();
    
    //Fetching value from interrupts
    int throttleRC = throttleTemp;
    int pitchRC = pitchTemp;
    int yawRC = yawTemp;
    int rollRC = rollTemp;
  
    //Allow interrupts again
    interrupts();
    
    //Scale it to the proper range
    throttleRC = generatePWM(throttleRC, throttleStart, throttleEnd, minPWM, maxPWM); 
    pitchRC = generatePWM(pitchRC, pitchStart, pitchEnd, minPWM, maxPWM); 
    yawRC = generatePWM(yawRC, yawStart, yawEnd, minPWM, maxPWM); 
    rollRC = generatePWM(rollRC, rollStart, rollEnd, minPWM, maxPWM); 
  
    //Read from MPU9250
    if (imu.Read()){
      ax = imu.accel_x_mps2() - axBias; ay = imu.accel_y_mps2() - ayBias; az = imu.accel_z_mps2();
      gx = imu.gyro_x_radps() - gxBias; gy = imu.gyro_y_radps() - gyBias; gz = imu.gyro_z_radps() - gzBias;
    }

    // Invert az to correct the negative gravity vector
    float corrected_az = -az;

    //Calculate angles from accelerometer
    accelPitch = atan2(ax, sqrt(ay * ay + corrected_az * corrected_az)) * radToDeg;
    accelRoll  = -atan2(ay, corrected_az) * radToDeg;

    // Gyro Pitch rate converted to degrees
    gyroPitch = gy * radToDeg;
    gyroRoll = gx * radToDeg;
    gyroYaw = gz * radToDeg;

    // Initialize angles on the very first run
    if (!flight) {
      currentPitchAngle = accelPitch;
      currentRollAngle = accelRoll;
      currentYawAngle = gyroYaw;
      flight = true;
      currentYawAngle = 0.0f;
    } 
    else {
      //Complementary Filter
      currentPitchAngle = 0.95f * (currentPitchAngle + gyroPitch * dt) + 0.05f * accelPitch;
      currentRollAngle  = 0.95f * (currentRollAngle  + gyroRoll * dt)  + 0.05f * accelRoll;
      currentYawAngle += (gyroYaw * dt);
    }
      
    //Convert receiver signals to degrees
    float targetPitchAngle = constrain(mapF(pitchRC, minPWM, maxPWM, minTilt, maxTilt), minTilt, maxTilt);
    float targetYawAngle   = constrain(mapF(yawRC, minPWM, maxPWM, minTilt, maxTilt), minTilt, maxTilt);
    float targetRollAngle  = constrain(mapF(rollRC, minPWM, maxPWM, minTilt, maxTilt), minTilt, maxTilt);

    //Reset PID if throttle goes too low to avoid integral buildup while on the ground
    if (throttleRC < 1050){
      pitchAngleIntegral = 0; pitchRateIntegral = 0;
      rollAngleIntegral = 0; rollRateIntegral = 0;
      yawAngleIntegral = 0;
      flight = false;
    }

    //Cascaded PID loop
    float targetPitchRate = calculatePID(targetPitchAngle, currentPitchAngle, pitchAngleIntegral, pitchAngleLastError, pitchAngleKp, pitchAngleKi, pitchAngleKd, dt);
    pidPitch = round(calculatePID(targetPitchRate, gyroPitch, pitchRateIntegral, pitchRateLastError, pitchRateKp, pitchRateKi, pitchRateKd, dt));

    float targetRollRate = calculatePID(targetRollAngle, currentRollAngle, rollAngleIntegral, rollAngleLastError, rollAngleKp, rollAngleKi, rollAngleKd, dt);
    pidRoll = round(calculatePID(targetRollRate, gyroRoll, rollRateIntegral, rollRateLastError, rollRateKp, rollRateKi, rollRateKd, dt));

    pidYaw = round(calculatePID(targetYawAngle, currentYawAngle, yawAngleIntegral, yawAngleLastError, yawAngleKp, yawAngleKi, yawAngleKd, dt));
  
    //Send motor pulses
    checkCrash();
    if (motorsEnabled && (flight == true)) {
        mixMotors(throttleRC, pidPitch, pidYaw, pidRoll);
    }
    else {
        esc1.writeMicroseconds(minPWM);
        esc2.writeMicroseconds(minPWM);
        esc3.writeMicroseconds(minPWM);
        esc4.writeMicroseconds(minPWM);
        flight = false;
    }

    /*
    //Print results
    Serial.print("Throttle Signal: ");
    Serial.print(throttleRC);
    Serial.print(" us");
    Serial.print(" | ");
    Serial.print("Pitch Signal: ");
    Serial.print(pitchRC);
    Serial.print(" us");
    Serial.print(" | ");
    Serial.print("Yaw Signal: ");
    Serial.print(yawRC);
    Serial.print(" us");
    Serial.print(" | ");
    Serial.print("Roll Signal: ");
    Serial.print(rollRC);
    Serial.print(" us");
    Serial.print(" | ");
    Serial.println();
    
    delay(100); //Delay to keep serial monitor
    */

    /*
    Serial.print("Pitch: "); Serial.print(currentPitchAngle, 2);
    Serial.print(" | Roll: "); Serial.println(currentRollAngle, 2);
    */
    
  }
  
  
}

//Receiver Main Function
void readPWM(int pin, volatile unsigned long &startTime, volatile int &value) {
  if (digitalRead(pin) == HIGH) {
    startTime = micros();
  } else {
    if (startTime != 0) {
      int pulseTime = micros() - startTime;
      if (pulseTime > 800 && pulseTime < 2200) { //Basic filtering  
        value = pulseTime;
      }
    }
  }
}

//Receiver Channel Functions
void readThrottle() { readPWM(throttlePin, throttlePWMStart, throttleTemp); }
void readPitch()    { readPWM(pitchPin, pitchPWMStart, pitchTemp); }
void readYaw()      { readPWM(yawPin, yawPWMStart, yawTemp); }
void readRoll()     { readPWM(rollPin, rollPWMStart, rollTemp); }



//Scale the transmitter values to the motor
int generatePWM(int rawValue, float oldRangeStart, float oldRangeEnd, float newRangeStart, float newRangeEnd){
  float result = mapF(rawValue, oldRangeStart, oldRangeEnd, newRangeStart, newRangeEnd);
  result = constrain(result, newRangeStart, newRangeEnd);
  return round(result);
}

//Fix yaw once it gets to hover
void mixMotors(int throttleRC, float pid_pitch, float pid_yaw, float pid_roll) {
  //Quad-X matrix (I am going counterclockwise)
  int m1_speed = throttleRC - pid_roll - pid_pitch - pid_yaw; // Front-Right
  int m2_speed = throttleRC - pid_roll + pid_pitch + pid_yaw; // Front-Left
  int m3_speed = throttleRC + pid_roll + pid_pitch - pid_yaw; // Rear-Left
  int m4_speed = throttleRC + pid_roll - pid_pitch + pid_yaw; // Rear-Right
  

  //Constrain
  m1_speed = constrain(m1_speed, minPWM, maxPWM);
  m2_speed = constrain(m2_speed, minPWM, maxPWM);
  m3_speed = constrain(m3_speed, minPWM, maxPWM);
  m4_speed = constrain(m4_speed, minPWM, maxPWM);

  //Send pulses
  esc1.writeMicroseconds(m1_speed);
  esc2.writeMicroseconds(m2_speed);
  esc3.writeMicroseconds(m3_speed); 
  esc4.writeMicroseconds(m4_speed);
}

float calculatePID(float target, float current, float &integral, float &lastError, float kp, float ki, float kd, float dt) {
  if (dt <= 0.0) return 0.0;
  // Calculate error
  float error = target - current;

  // Calculate Integral
  integral += error * dt;
  integral = constrain(integral, pidPWMMin, pidPWMMax);

  // Calculate Derivative
  float derivative = (error - lastError) / dt;
  lastError = error; 

  // Add to make the final controller: P + I + D
  float output = (kp * error) + (ki * integral) + (kd * derivative);
  
  return constrain(output, pidPWMMin, pidPWMMax);
}

float mapF(float x, float in_min, float in_max, float out_min, float out_max) {
  return (x - in_min) * (out_max - out_min) / (in_max - in_min) + out_min;
}


//Set Flight Mode 
void setFlightMode(char mode){
  if(mode == 'N'){
    maxFlightSpeed = 0.7;
  }
  else if(mode == 'C'){
    maxFlightSpeed = 0.6;
  }
  else if (mode == 'S'){
    maxFlightSpeed = 1.0;
  }
}

void checkCrash() {
  if (abs(currentRollAngle) > 70 ||
      abs(currentPitchAngle) > 70 ||
      abs(gyroRoll) > 500 ||
      abs(gyroPitch) > 500) {

    motorsEnabled = false;
  }
}

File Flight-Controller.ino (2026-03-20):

#include <SPI.h>
#include <Wire.h>
#include <MPU6050.h>

//MPU
MPU6050 mpu; //I am using mpu6050 cause I have that with me so I can test with it. After I recieve my mpu9250, I'll update the code to use that. 

bool initialized = false;

// Timing
unsigned long prevTime = 0;
unsigned long lastDisplay = 0;

// Angles
float roll = 0;
float pitch = 0;
float yaw = 0;

// Accel angles
float accel_roll = 0;
float accel_pitch = 0;

//Motor libraries
#include <Servo.h>
#include <IBusBM.h>

//Define 4 motors
Servo motor1;
Servo motor2;
Servo motor3;
Servo motor4;

//Define bus for radio communication
IBusBM iBus;

//Flight state
bool flight = false;
int motor1_speed = 0;
int motor2_speed = 0;
int motor3_speed = 0;
int motor4_speed = 0;

void setup() {
  Serial.begin(115200);

  while (!mpu.begin(MPU6050_SCALE_2000DPS, MPU6050_RANGE_8G)) { //2000 degrees and 8G
    Serial.println("Sensor not found!");
    delay(500);
  }
  mpu.setDLPFMode(MPU6050_DLPF_4); 

  // Gyro calibration
  mpu.calibrateGyro();
  mpu.setThreshold(0);

  prevTime = millis();

  iBus.begin(Serial);
  
  //Connect wires (pin 3,4,5,6)
  motor1.attach(3);
  motor2.attach(4);
  motor3.attach(5);
  motor4.attach(6);

  //Ground drone
  ground();
  
  //Wait 3 seconds for initialization
  delay(3000);
}

void loop() {
  unsigned long now = millis();
  float dt = (now - prevTime) / 1000.0;
  prevTime = now;

  // Read sensors
  Vector gyro = mpu.readNormalizeGyro();
  Vector accel = mpu.readNormalizeAccel();

  // Compute accel angles
  accel_roll = atan2(accel.YAxis, accel.ZAxis) * 180.0 / M_PI;
  accel_pitch = -atan2(accel.XAxis, sqrt(accel.YAxis * accel.YAxis + accel.ZAxis * accel.ZAxis)) * 180.0 / M_PI;

  // Initialize
  if (!initialized) {
    roll = accel_roll;
    pitch = accel_pitch;
    yaw = 0;
    initialized = true;
  } 
  
  else {
    float alpha = 0.98;

    //sensor fusion
    roll = alpha * (roll + gyro.XAxis * dt) + (1 - alpha) * accel_roll;
    pitch = alpha * (pitch + gyro.YAxis * dt) + (1 - alpha) * accel_pitch;

    //Yaw
    yaw += gyro.ZAxis * dt;
  }

  /*
    -If the stick is at the very bottom: The value will be ~1000.
    -If the stick is halfway up: The value will be ~1500.
    -If the stick is at the very top: The value will be ~2000.
  */
  //I am guessing this information based on the internet, but the truth will unveil when I actually test the reciever and transmitter
  int altitude = iBus.readChannel(2);
  int rotation = iBus.readChannel(3);
  int lr = iBus.readChannel(0);
  int fb = iBus.readChannel(1);

  

  //Up and down
  //=========================================================================
  if(abs(altitude - 1500) < 10){
    if(!flight){
      ground();
    }
    else{
      //This is when drone is stable in the air
      stabilize(roll, pitch, gyro, dt, motor1_speed, motor2_speed, motor3_speed, motor4_speed);
    }
  }
  
  else{
    if(altitude >= 1510){
      motor1_speed = map(altitude, 1510, 2000, 50, 100);
      motor2_speed = map(altitude, 1510, 2000, 50, 100);
      motor3_speed = map(altitude, 1510, 2000, 50, 100);
      motor4_speed = map(altitude, 1510, 2000, 50, 100);
      update_speed();

      //Toggle flight mode
      flight = true;
    }
    if(altitude <= 1490){
      if(flight){
        motor1_speed = map(altitude, 1000, 1490, 0, 50);
        motor2_speed = map(altitude, 1000, 1490, 0, 50);
        motor3_speed = map(altitude, 1000, 1490, 0, 50);
        motor4_speed = map(altitude, 1000, 1490, 0, 50);
        update_speed(); 
      }
    }
    else{
      return;
    }
  }
  //=========================================================================


  //Rotation
  //=========================================================================
  if(rotation > 1500){
    //***20% increase/decrease for rotation
    motor1_speed += 20;
    motor2_speed -= 20;
    motor3_speed += 20;
    motor4_speed -= 20;
    update_speed();
  }
  if(rotation < 1500){
    motor1_speed -= 20;
    motor2_speed += 20;
    motor3_speed -= 20;
    motor4_speed += 20;
    update_speed();
  }
  //=========================================================================

  //Left/Right
  //=========================================================================
  if(lr > 1500){
    //***20% increase/decrease for left/right
    motor1_speed -= 20;
    motor2_speed -= 20;
    motor3_speed += 20;
    motor4_speed += 20;
    update_speed();
  }
  if(lr < 1500){
    motor1_speed += 20;
    motor2_speed += 20;
    motor3_speed -= 20;
    motor4_speed -= 20;
    update_speed();
  }
  //=========================================================================

  //Front/Back
  //=========================================================================
  if(fb > 1500){
    //***20% increase/decrease for front/back
    motor1_speed -= 20;
    motor2_speed += 20;
    motor3_speed += 20;
    motor4_speed -= 20;
    update_speed();
  }
  if(fb < 1500){
    motor1_speed += 20;
    motor2_speed -= 20;
    motor3_speed -= 20;
    motor4_speed += 20;
    update_speed();
  }
  //=========================================================================

  //Check for speed to ground
  if(motor1_speed <= 10 || motor2_speed <= 10 || motor3_speed <= 10 || motor4_speed <= 10){
    ground();
    flight = false;
  }

}

//Stabilizing function
void stabilize(float roll, float pitch, Vector gyro, float dt, int &motor1_speed, int &motor2_speed, int &motor3_speed, int &motor4_speed) {
  //This is a basic stabilize loop to control the drone while in stabilization

  
  //PID constants, tune later after physically building the drones
  float Kp = 1.5;
  float Ki = 0.0;
  float Kd = 0.5;

  //0* for stability
  float target_roll = 0;
  float target_pitch = 0;

  
  float integral_roll = 0;
  float integral_pitch = 0;

  float prev_error_roll = 0;
  float prev_error_pitch = 0;

  float error_roll = target_roll - roll;
  float error_pitch = target_pitch - pitch;

  //Integrate
  integral_roll += error_roll * dt;
  integral_pitch += error_pitch * dt;


  //Derivative
  float d_roll = -gyro.XAxis;
  float d_pitch = -gyro.YAxis;

  //PID = P + I + D
  float roll_output  = Kp * error_roll  + Ki * integral_roll  + Kd * d_roll;
  float pitch_output = Kp * error_pitch + Ki * integral_pitch + Kd * d_pitch;

  //Motor output
  motor1_speed = motor1_speed - roll_output + pitch_output;
  motor2_speed = motor2_speed + roll_output + pitch_output;
  motor3_speed = motor3_speed + roll_output - pitch_output;
  motor4_speed = motor4_speed - roll_output - pitch_output;

  //control it to 100%
  motor1_speed = constrain(motor1_speed, 0, 100);
  motor2_speed = constrain(motor2_speed, 0, 100);
  motor3_speed = constrain(motor3_speed, 0, 100);
  motor4_speed = constrain(motor4_speed, 0, 100);

  //Update motors
  update_speed();
}


//Set speed of the motors
void set_speed(Servo &motor, int throttle){
  int ms = map(throttle, 0, 100, 1000, 2000);
  motor.writeMicroseconds(ms);
  delay(5);
}
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

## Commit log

2026-03-18 Clarify drone's camera usage in README
    Updated description for clarity on drone's functionality.
2026-03-23 Update drone frame cost and total cost
    Updated the cost of the drone frame from $15.00 to $22.00, resulting in a new total cost of $198.79 USD.
2026-03-23 Refine README content and remove unnecessary notes
    Removed redundant notes and improved clarity in the Bill of Materials section.
2026-04-12 PCB Layout
    [PCB.kicad_pcb, PCB.kicad_sch]
2026-04-18 Added PCB Files
    [PCB-B_Cu.gbr, PCB-B_Mask.gbr, PCB-B_Paste.gbr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]
2026-05-09 Add unzipping instructions for Final_Drone.step
    Add instructions for unzipping the Final_Drone.step file.
    [Final_Drone.step]
2026-06-03 updated pcb files
2026-06-10 Added new 3D files
    [Final_Drone.step, hackclub.f3d, hackclub.step]
2026-06-11 changed designs for chassis
    [hackclub.f3d, hackclub.step]
2026-06-11 added the proper files
    Last time I accidentally uploaded outdated files, these are the latest ones.
    [hackclub.f3d, hackclub.step]
2026-06-12 Added another hole to the arm for stability
    [hackclub.f3d, hackclub.step]
2026-06-12 CAD Arms Design Changes
    Made more changes to the drone arms including their thickness to make them much more sturdier to shocks and crashes. This should prove vital during testing.
    [hackclub.f3d, hackclub.step]
2026-06-13 Added curved shapes for improved aerodynamics
    [hackclub.f3d, hackclub.step]
2026-06-13 Added Brushless Motors
    [hackclub.f3d, hackclub.f3z]
2026-06-13 Renamed bom.csv
    [BOM.csv]
2026-06-14 Flipped Screw hole positions
    [hackclub.f3z]
2026-06-15 Replaced back
    [hackclub.f3z]
2026-06-15 Fixed motor wheels and added bumps for shock absorbers later
    [hackclub.f3z]
2026-06-18 Added Landing Legs
    Added proper landing legs with screw holes to attach it to the main body.
    [hackclub.f3d, hackclub.f3z]
2026-06-19 Revise Bill of Materials in README.md
    Updated the Bill of Materials section with additional components and corrected some entries.
2026-06-19 Update BOM.csv
    Updated BOM.csv with new parts and replaced or corrected old parts.
    [BOM.csv]
2026-06-19 Added an area for the electronics
    [PCB-B_Cu.gbr, PCB-B_Mask.gbr, PCB-B_Paste.gbr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]
2026-06-20 Made landing legs shorter to make drone more stable and resistant to toppling over
    [hackclub.f3d, hackclub.step]
2026-06-20 Fixed holes from m2 to m3, i accidentally switched them
    [hackclub.f3d, hackclub.step]
2026-06-26 Create MPU9250_IMU.ino
    Added a new IMU file for the updated MPU9250 instead of the old MPU6050
